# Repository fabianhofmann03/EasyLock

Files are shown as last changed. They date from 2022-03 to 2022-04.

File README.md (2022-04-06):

# EasyLock
EasyLock ist ein Schulprojekt von mir und 2 weiteren Kollegen.
Es nutzt einen magnetischen Schieberiegler der die Tür auf und zu sperrt und einen Hallsensor um den aktuellen Zustand der Tür zu erkennen.
Über eine App auf dem Handy kann das Schloss dann geöffnet, das Passwort geändert oder die Werte des Hallsensors konfiguriert werden.

# Protokoll

Das Projekt nutzt 4 verschiedene Nachrichten zum kommunizieren. Commands, Requests, Data und Status. 
Die ersten Bytes der Nachrichten bestehen aus den Indikatoren, die dem Programm sagen, was für eine Nachricht gesendet wurde. 
Am Ende jeder Nachricht wird ein Control Byte gesendet, das aus allen vorherigen Bytes der Nachricht, welche mit einer Bitweisen XOR Operation kombiniert wurden, besteht. 

## Command

| Command Protocol | | | | | | | | |
|---|---|---|---|---|---|---|---|---|
| Byte Name | Bit 8 | Bit 7 | Bit 6 | Bit 5 | Bit 4 | Bit 3 | Bit 2 | Bit 1 |
| Command Start | 1 | 0 | 0 | 0 | 0 | 0 | 0 | 1 |
| Command | x | x | x | x | x | x | x | x |
| Control Byte | x | x | x | x | x | x | x | x |

Der Command startet im Microcontroller eine Reihe an Befehlen die ausgeführt werden. Während des Befehls werden zwischen App und Microcontroller einige Request- und Data-Nachrichten ausgetauscht. Da der Microcontroller nur einen gewissen Speicherplatz hat, schickt dieser immer erst die Request, wenn er den Wert auch benötigt. Desshalb muss während dem Ausführen der Commands auch eine konstante Verbindung zwischen den Geräten herrschen.

Das zweite Byte besteht aus dem Command, der ausgeführt werden soll. Die Liste an ausführbaren Commands finden Sie hier:

| Command Byte | | | | | | | | | |
|---|---|---|---|---|---|---|---|---|---|
| Command | Bit 8 | Bit 7 | Bit 6 | Bit 5 | Bit 4 | Bit 3 | Bit 2 | Bit 1 | Description |
| Change Password | 0 | 0 | 0 | 0 | 0 | 0 | 0 | 1 | Change the Password of the Lock |
| Open Lock | 0 | 0 | 0 | 0 | 0 | 0 | 1 | 0 | Open the Lock |
| Start Config | 0 | 0 | 0 | 0 | 0 | 0 | 1 | 1 | Starts configuration of Hall Sensor |

## Request und Data

| Request Protocol | | | | | | | | |
|---|---|---|---|---|---|---|---|---|
| Byte Name | Bit 8 | Bit 7 | Bit 6 | Bit 5 | Bit 4 | Bit 3 | Bit 2 | Bit 1 |
| Request Start | 0 | 1 | 0 | 0 | 0 | 0 | 1 | 0 |
| Requested Variable | x | x | x | x | x | x | x | x |
| Control Byte | x | x | x | x | x | x | x | x |

Bei der Request wird von einem der Geräte ein Wert oder manchmal auch nur eine Status-Nachricht gewünscht.
Bei "Password" und "New Password" wird eine Data-Nachricht geschickt zurückgeschickt, bei "Lock Status" eine Status Nachricht.

Das zweite Byte besteht aus der Variable, die gewünscht wird. Dabei ist jedoch das höchstwertige Bit leer zu halten, da das das Flag Bit ist, das verwendet wird um zu erkennen, ob eine neue Request eingetroffen ist. Die Liste an Variablen finden am Ende dieses Abschnitts.

| Data Protocol | | | | | | | | |
|---|---|---|---|---|---|---|---|---|
| Byte Name | Bit 8 | Bit 7 | Bit 6 | Bit 5 | Bit 4 | Bit 3 | Bit 2 | Bit 1 |
| Data Start | 0 | 0 | 1 | 0 | 0 | 1 | 0 | 0 |
| Sent Variable | x | x | x | x | x | x | x | x |
| Data Length | x | x | x | x | x | x | x | x |
| Data | x | x | x | x | x | x | x | x |
| | x | x | x | x | x | x | x | x |
| | …… | …… | …… | …… | …… | …… | …… | …… |
| Control Byte | x | x | x | x | x | x | x | x |

Die Data-Nachricht versendet große Daten die für die Commads benötigt werden. Wegen des begrenzten Speichers des Microcontrollers wird die Länge auf 127 Bytes beschränkt. 

Im zweiten Byte ist gespeichert, welche Variable geschickt wurde. Wie bei der Request Nachricht ist das höchstwertige Bit leer zu halten. Die möglichen Variablen finden Sie am Ende dieses Abschnitts.
Im dritten Byte ist gespeichert, wie viele Bytes an Daten geschickt werden. 
In den folgenden Bits sind dann die Daten gespeichert.

| Variable Name | | | | | | | | | |
|---|---|---|---|---|---|---|---|---|---|
| Variable Name | Bit 8 | Bit 7 | Bit 6 | Bit 5 | Bit 4 | Bit 3 | Bit 2 | Bit 1 | Function |
| Password | 0 | 0 | 0 | 0 | 0 | 0 | 0 | 1 | Current Password of the lock |
| New Password  | 0 | 0 | 0 | 0 | 0 | 0 | 1 | 0 | New Password for the lock |
| Lock Status | 0 | 0 | 0 | 0 | 0 | 0 | 1 | 1 | Status of the Lock |

## Status

| Status Protocol | | | | | | | | |
|---|---|---|---|---|---|---|---|---|
| Byte Name | Bit 8 | Bit 7 | Bit 6 | Bit 5 | Bit 4 | Bit 3 | Bit 2 | Bit 1 |
| Status Start | 0 | 0 | 0 | 1 | 1 | 0 | 0 | 0 |
| Status Message | x | x | x | x | x | x | x | x |

Die Status Nachricht ist eine kurze Nachricht, welche keine spezielle Funktion hat. Beispiel hierfür sind Error-Messages, Bestätigungen für erhaltene Commands/Requests/Daten, oder auch aktuellen Status des Schlosses. 

Die Status-Nachricht hat kein Controll Byte, desshalb besteht sie nur aus dem Indikator und der Status Message.
Status-Messages die versendet werden können finden Sie hier: 

| Status Message | | | | | | | | | |
|---|---|---|---|---|---|---|---|---|---|
| Status Name | Bit 8 | Bit 7 | Bit 6 | Bit 5 | Bit 4 | Bit 3 | Bit 2 | Bit 1 | Description |
| Command executed  | 0 | 0 | 0 | 0 | 0 | 0 | 0 | 1 | The wanted command is finished. No more information needed |
| Received | 0 | 0 | 0 | 0 | 0 | 0 | 1 | 0 | Request or data received successfully |
| Deny | 0 | 0 | 0 | 0 | 0 | 0 | 1 | 1 | Command denied |
| Too much data | 0 | 0 | 0 | 0 | 0 | 1 | 0 | 0 | Too much data was sent. Can't process |
| Message corrupted | 0 | 0 | 0 | 0 | 0 | 1 | 0 | 1 | Message was corrupted while sending. Please repeat |
| Lock opened | 0 | 0 | 0 | 0 | 0 | 1 | 1 | 0 | Lock is currently open |
| Lock closed | 0 | 0 | 0 | 0 | 0 | 1 | 1 | 1 | Lock is currently closed |
| Cancel | 0 | 0 | 0 | 0 | 1 | 0 | 0 | 0 | Cancel Command |
| Continue | 0 | 0 | 0 | 0 | 1 | 0 | 0 | 1 | Continue Command |

## Kommunikation

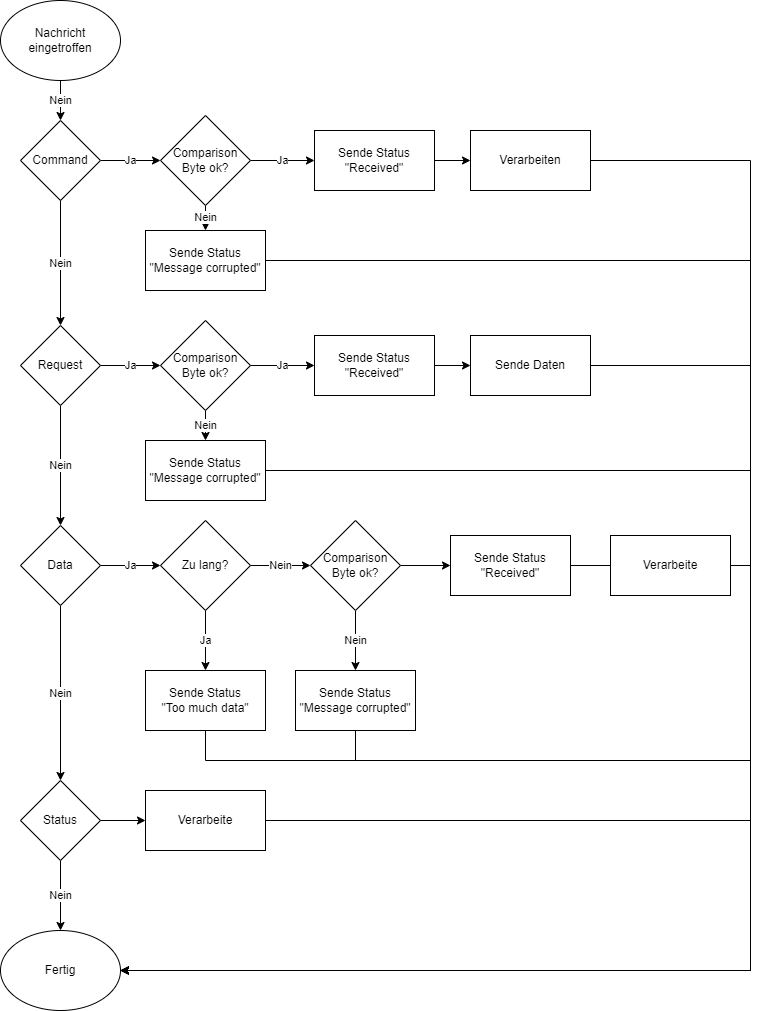
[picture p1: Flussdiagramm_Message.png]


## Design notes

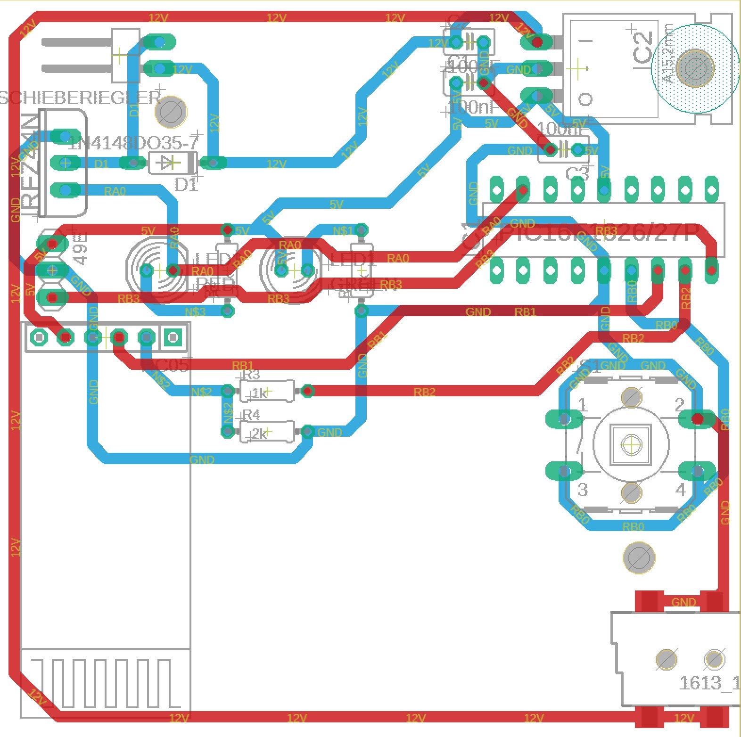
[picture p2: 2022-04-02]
Schaltung & Platine/Platine.jpg

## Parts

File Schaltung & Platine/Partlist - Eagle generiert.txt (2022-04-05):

Partlist

Exported from EasyLock.brd at 05.04.2022 14:36

EAGLE Version 9.6.2 Copyright (c) 1988-2020 Autodesk, Inc.

Assembly variant: 

Part           Value          Package      Library      Position (mm)         Orientation

49E                           1X03         pinhead      (5.08 44.45)          R270
C1             100nF          C025-025X050 rcl          (44.45 62.23)         R0
C2             100nF          C025-025X050 rcl          (44.45 66.04)         R0
C3             100nF          C025-025X050 rcl          (53.34 55.88)         R180
D1             1N4148DO35-7   DO35-7       diode        (16.51 54.61)         R180
HC05                          1X06         HC05         (10.16 38.1)          R180
IC1            PIC16F1826/27P DIL18        microchip    (57.15 48.26)         R0
IC2                           78XXL        v-reg        (54.61 63.5)          R270
IRFZ44N                       TO-220       IRFZ44N      (6.35 54.61)          R90
LED1           GREEN          LED5MM       led          (27.94 44.45)         R0
LED2           RED            LED5MM       led          (15.24 44.45)         R0
R1             1k             0204/7       rcl          (34.29 44.45)         R90
R2             1k             0204/7       rcl          (21.59 44.45)         R90
R3             1k             0204/7       rcl          (25.4 33.02)          R0
R4             2k             0204/7       rcl          (25.4 29.21)          R0
S1                            B3F-40XX     switch-omron (59.69 27.94)         R0
SCHIEBERIEGLER                1X02/90      pinhead      (11.43 64.77)         R90
X1             1613_14        1613_14      con-lumberg  (72.546028125 7.704575) R90

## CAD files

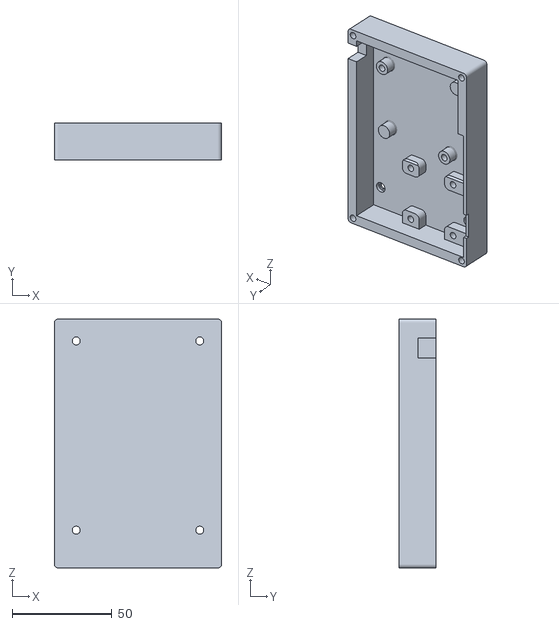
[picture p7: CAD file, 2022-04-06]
3D-Druck Dateien/gehäuse.stl
84.0 x 18.6 x 125.0

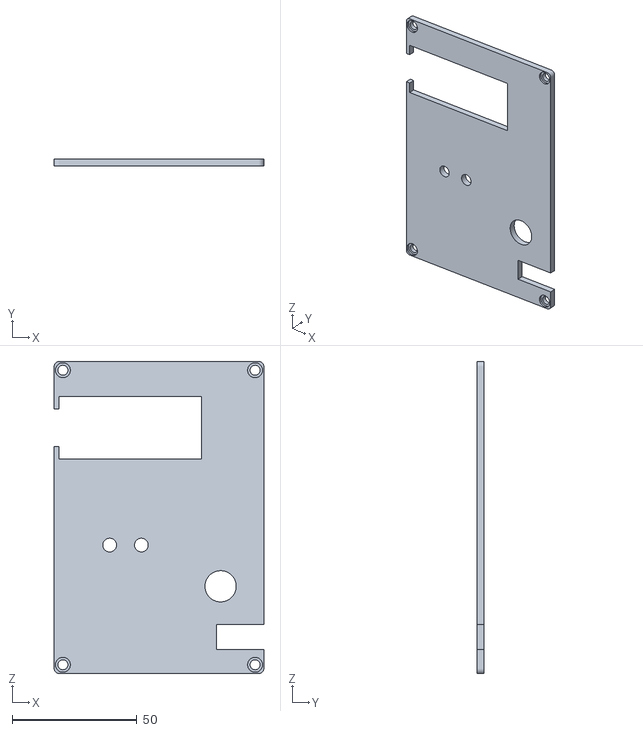
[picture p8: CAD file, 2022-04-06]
3D-Druck Dateien/deckel.stl
84.0 x 3.00 x 125.0

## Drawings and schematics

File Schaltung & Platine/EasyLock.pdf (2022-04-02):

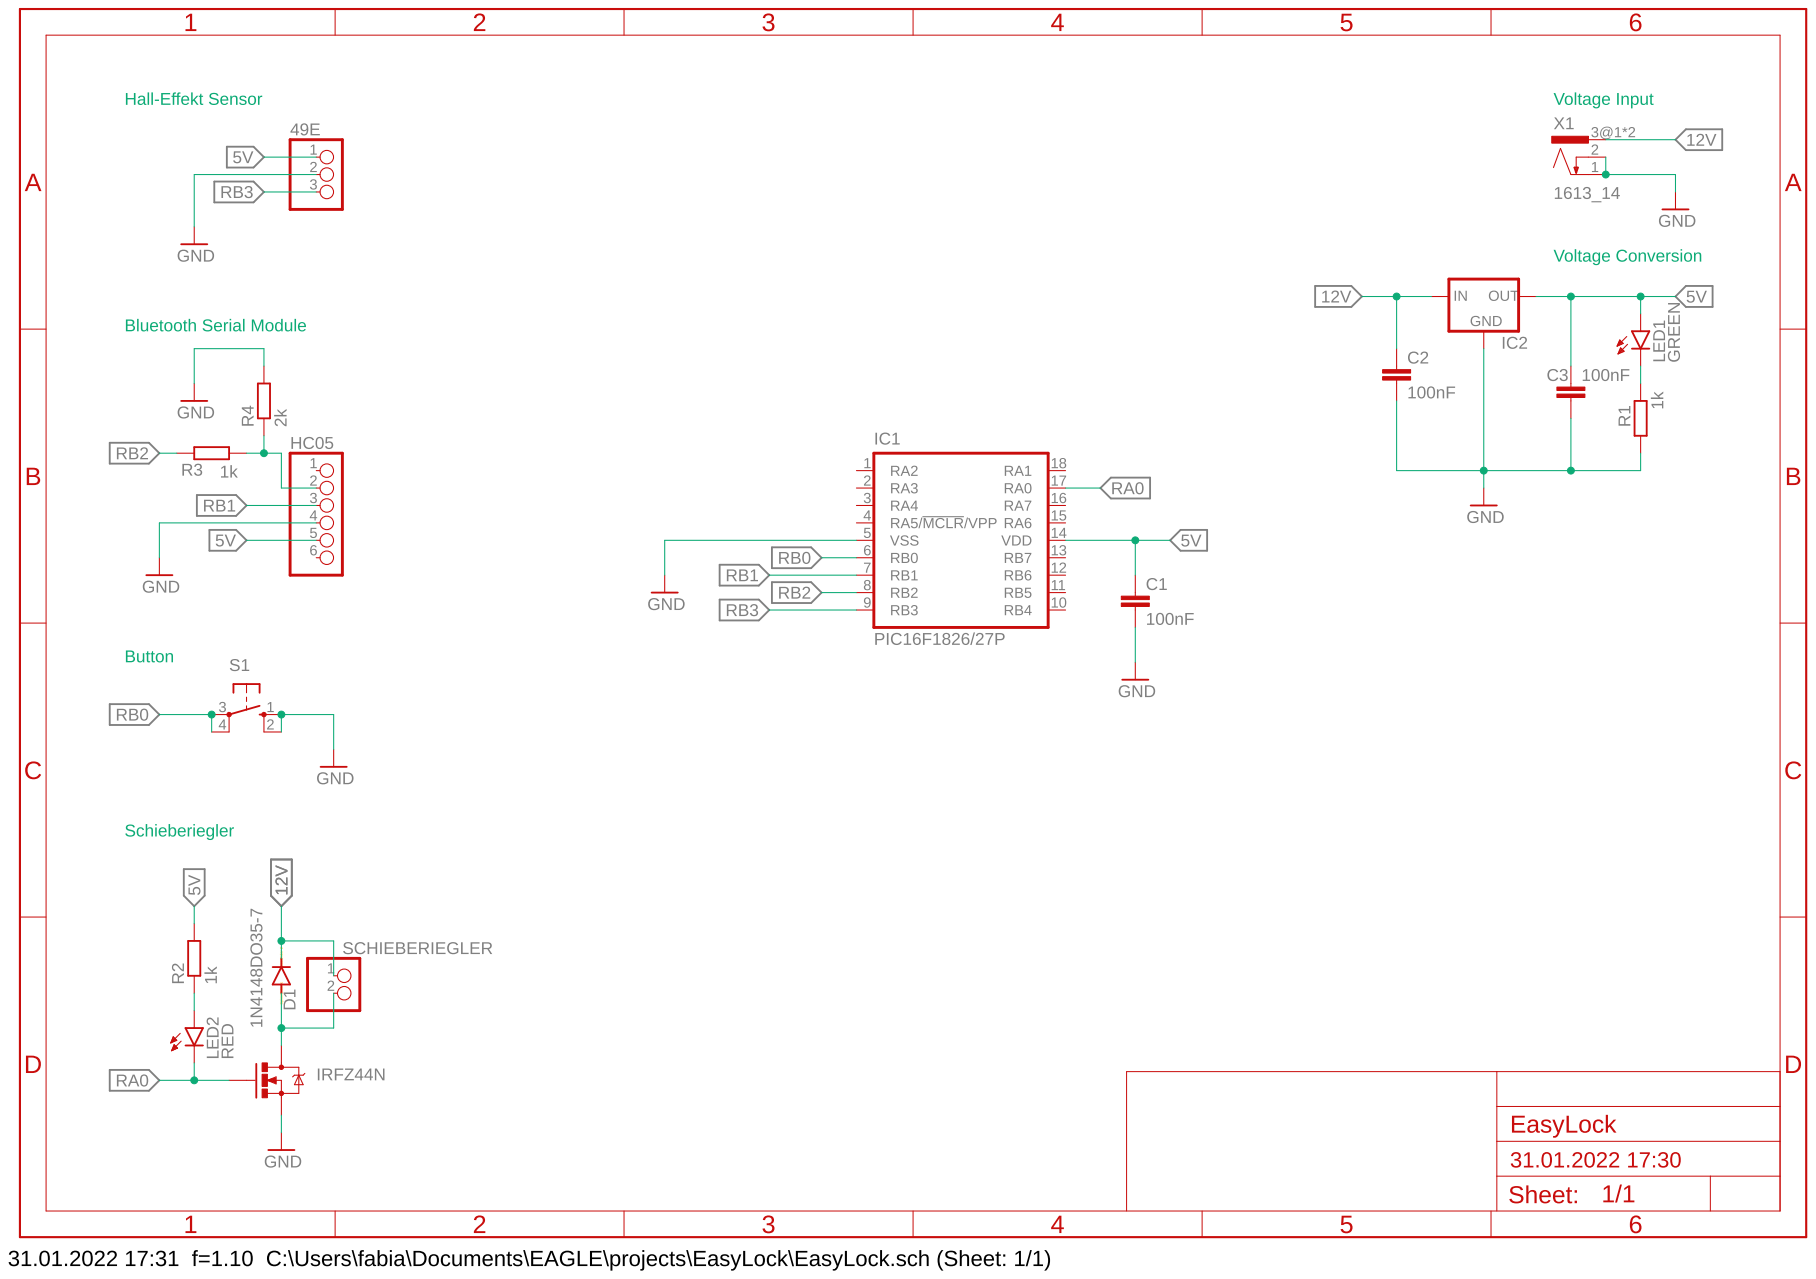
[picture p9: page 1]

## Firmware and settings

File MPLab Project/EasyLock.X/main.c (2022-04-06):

/**
  Generated Main Source File

  Company:
    Microchip Technology Inc.

  File Name:
    main.c

  Summary:
    This is the main file generated using PIC10 / PIC12 / PIC16 / PIC18 MCUs

  Description:
    This header file provides implementations for driver APIs for all modules selected in the GUI.
    Generation Information :
        Product Revision  :  PIC10 / PIC12 / PIC16 / PIC18 MCUs - 1.81.7
        Device            :  PIC16F1827
        Driver Version    :  2.00
 */

/*
    (c) 2018 Microchip Technology Inc. and its subsidiaries. 
    
    Subject to your compliance with these terms, you may use Microchip software and any 
    derivatives exclusively with Microchip products. It is your responsibility to comply with third party 
    license terms applicable to your use of third party software (including open source software) that 
    may accompany Microchip software.
    
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
    IN NO EVENT WILL MICROCHIP BE LIABLE FOR ANY INDIRECT, SPECIAL, PUNITIVE, 
    INCIDENTAL OR CONSEQUENTIAL LOSS, DAMAGE, COST OR EXPENSE OF ANY KIND 
    WHATSOEVER RELATED TO THE SOFTWARE, HOWEVER CAUSED, EVEN IF MICROCHIP 
    HAS BEEN ADVISED OF THE POSSIBILITY OR THE DAMAGES ARE FORESEEABLE. TO 
    THE FULLEST EXTENT ALLOWED BY LAW, MICROCHIP'S TOTAL LIABILITY ON ALL 
    CLAIMS IN ANY WAY RELATED TO THIS SOFTWARE WILL NOT EXCEED THE AMOUNT 
    OF FEES, IF ANY, THAT YOU HAVE PAID DIRECTLY TO MICROCHIP FOR THIS 
    SOFTWARE.
 */

#include "mcc_generated_files/mcc.h"
#include <stdio.h>
#include <stdlib.h>

#define data_storage_size 127
#define password_position 4

#define receive_timer_time 50
#define cmd_timer_time 1000
#define continue_time 12000
#define button_timer_time 50


/*
                         Main application
 */

enum lockstates {
    IDLE, OPENLOCK, WAITFOROPEN, WAITFORCLOSE
};
enum lockstates working_state = IDLE;

enum commandcontroll {
    WAITFORCMD, READCMD, READREQ, READDATLEN, READDATVAR, READDAT, READSTAT, COMP
};
enum commandcontroll cmd_state = WAITFORCMD;

enum commandexecution {
    WAITTOSTART, EXECMD
};
enum commandexecution cmd_exe = WAITTOSTART;

enum command {
    CHANGE_PASSWORD = 1, OPEN_LOCK = 2, START_CONFIG = 3
};

enum variable {
    PASSWORD = 1, NEW_PASSWORD = 2, LOCK_STATUS = 3
};

enum status_message {
    COMMAND_EXECUTED = 1, RECEIVED = 2, DENY = 3, TOO_MUCH_DATA = 4, MESSAGE_CORRUPTED = 5, LOCK_OPEND = 6, LOCK_CLOSED = 7, CANCELD = 8, CONTINUE = 9
};

uint8_t cmd;
uint8_t data_storage[data_storage_size + 2];                //First byte:   [xxxxxxxx]
                                                            //              [x-------] 1: Data completly loaded, 0: Data still loading
                                                            //              [-xxxxxxx] What variable is stored
                                                            //Second byte:  [xxxxxxxx] Length of Data (max 127)

uint8_t request_storage;                                    //  [x-------] 1: Request has come, 0: No request
                                                            //  [-xxxxxxx] Requested Variable

uint8_t status_storage;                                     //  [x-------] 1: State has come, 0: No state
                                                            //  [-xxxxxxx] Last State

uint8_t hall_codes[] = {127, 103};                          // 1: Open door
                                                            // 2: Closed door

int cmd_exe_counter = 0;
bool lock_status = false;

uint8_t new_hall_code_open = 0;
uint8_t new_hall_code_close = 0;

void del_array(uint8_t *array, int16_t len);

void send_msg_stopping(uint8_t *msg, uint8_t len);
void send_cmd(uint8_t cmd);
void send_req(uint8_t var);
void send_dat(uint8_t *dat, uint8_t len, uint8_t var);
void send_stat(uint8_t stat);
bool compare_pw(uint8_t *pw, uint8_t len);
void save_pw(uint8_t *pw, uint8_t len);
void read_hall_codes(void);
void save_hall_codes(uint8_t open, uint8_t close);
bool wait_for_requested(uint8_t req);
void stop_cmd(void);
int seek_confirmation(int wait_num, int continue_num, int retry_num, int cancel_num);
bool door_status_changed(bool open_or_close, int16_t val);

long receive_time = 0;
long receive_timer_len = 0;
long cmd_time = 0;
long cmd_timer_len = 0;
long button_time = 0;
bool button_status = false;
bool button = false;

void timer_up() {
    if(receive_timer_len > 0) receive_time++;
    if(cmd_timer_len > 0) cmd_time++;
    if(button_status) button_time++;
    button = !BUTTON_GetValue();
    if(button != button_status) {
        if(button_status && button_time < button_timer_time) {
            if(lock_status) {
                working_state = WAITFORCLOSE;
            }else {
                working_state = OPENLOCK;
            }
        }else {
            button_time = 0;
        }
    }
    button_status = button;
}

void main(void) {
    // initialize the device
    SYSTEM_Initialize();
    EUSART_Initialize();
    ADC_Initialize();
    TMR2_Initialize();

    // When using interrupts, you need to set the Global and Peripheral Interrupt Enable bits
    // Use the following macros to:

    // Enable the Global Interrupts
    INTERRUPT_GlobalInterruptEnable();

    // Enable the Peripheral Interrupts
    INTERRUPT_PeripheralInterruptEnable();

    ADC_StartConversion();
    TMR2_SetInterruptHandler(timer_up);
    
    read_hall_codes();
    
    while (1) {
        if(receive_timer_len > 0 && receive_time > receive_timer_len) {
            receive_time = 0;
            receive_timer_len = 0;
            stop_cmd();
        }
        if(cmd_timer_len > 0 && cmd_time > cmd_timer_len) {
            send_stat(CANCELD);
            stop_cmd();
        }
        if (EUSART_is_rx_ready()) {
            receive_timer_len = receive_timer_time;
            receive_time = 0;
            uint8_t input = EUSART_Read();
            static uint8_t control_byte;
            static uint8_t data_storage_counter = 0;
            static enum commandcontroll last_state = WAITFORCMD;
            switch (cmd_state) {
                case WAITFORCMD:
                    last_state = cmd_state;
                    if (input == 0b10000001) cmd_state = READCMD;
                    else if (input == 0b01000010) cmd_state = READREQ;
                    else if (input == 0b00100100) cmd_state = READDATVAR;
                    else if (input == 0b00011000) cmd_state = READSTAT;
                    control_byte = input;
                    break;
                case READCMD:
                    cmd = input;
                    last_state = cmd_state;
                    cmd_state = COMP;
                    break;
                case READREQ:
                    request_storage = input;
                    last_state = cmd_state;
                    cmd_state = COMP;
                    break;
                case READDATVAR:
                    data_storage[0] = input;
                    last_state = cmd_state;
                    cmd_state = READDATLEN;
                    break;
                case READDATLEN:
                    data_storage[1] = input;
                    last_state = cmd_state;
                    cmd_state = READDAT;
                    if(data_storage[1] == 0) cmd_state = COMP;
                    break;
                case READDAT:
                    if (data_storage[1] <= data_storage_size) data_storage[data_storage_counter + 2] = input;
                    data_storage_counter++;
                    if (data_storage_counter == (data_storage[1])) {
                        data_storage_counter = 0;
                        last_state = cmd_state;
                        cmd_state = COMP;
                    }
                    break;
                case READSTAT:
                    status_storage = input;
                    last_state = cmd_state;
                    status_storage = status_storage | (1<<7);
                    cmd_state = WAITFORCMD;
                    receive_timer_len = 0;
                    break;
                case COMP:
                    if (control_byte == input) {
                        switch (last_state) {
                            case READCMD:
                                if (control_byte != input) {
                                    send_stat(MESSAGE_CORRUPTED);
                                } else {
                                    stop_cmd();
                                    send_stat(RECEIVED);
                                    cmd_exe = EXECMD;
                                }
                                break;
                            case READREQ:
                                if (control_byte != input) {
                                    send_stat(MESSAGE_CORRUPTED);
                                } else {
                                    send_stat(RECEIVED);
                                    request_storage = request_storage | (1 << 7);
                                }
                                break;
                            case READDAT:
                                if (data_storage[1] > data_storage_size) {
                                    send_stat(TOO_MUCH_DATA);
                                } else if (control_byte != input) {
                                    send_stat(MESSAGE_CORRUPTED);
                                } else {
                                    send_stat(RECEIVED);
                                    data_storage[0] = data_storage[0] | (1 << 7);
                                }
                                break;
                            case READDATLEN:
                                if (data_storage[1] > data_storage_size) {
                                    send_stat(TOO_MUCH_DATA);
                                } else if (control_byte != input) {
                                    send_stat(MESSAGE_CORRUPTED);
                                } else {
                                    send_stat(RECEIVED);
                                    data_storage[0] = data_storage[0] | (1 << 7);
                                }
                                break;
                        }
                    }
                    last_state = cmd_state;
                    cmd_state = WAITFORCMD;
                    receive_timer_len = 0;
                    receive_time = 0;
                    break;
            }
            if (last_state != WAITFORCMD) control_byte = control_byte ^ input;
        }
        
        if((status_storage & (1<<7)) > 0) {
            switch(status_storage & (~(1<<7))) {
                case CANCELD:
                    if(lock_status == true) {
                        ADC_StartConversion();
                        working_state = WAITFORCLOSE;
                    }
                    stop_cmd();
                    status_storage = status_storage & (~(1<<7));
                    break;
            }
        }
        if((request_storage & (1<<7)) > 0) {
            switch(request_storage & (~(1<<7))) {
                case LOCK_STATUS:
                    if(lock_status) {
                        send_stat(LOCK_OPEND);
                    }else {
                        send_stat(LOCK_CLOSED);
                    }
                    request_storage = status_storage & (~(1<<7));
                    break;
            }
        }
        static int old_cmd_exe_counter = 0;
        switch (cmd_exe) {
            case WAITTOSTART:
                    cmd_timer_len = 0;
               break;
            case EXECMD:
                if(old_cmd_exe_counter != cmd_exe_counter) {
                    cmd_time = 0;
                    cmd_timer_len = cmd_timer_time;
                }
                old_cmd_exe_counter = cmd_exe_counter;
                switch (cmd) {
                    case CHANGE_PASSWORD:
                        switch (cmd_exe_counter) {
                            case 0:
                                send_req(PASSWORD);
                                cmd_exe_counter++;
                                break;
                            case 1:
                                cmd_exe_counter = seek_confirmation(1, 2, 0, 255);
                                break;
                            case 2:
                                if(wait_for_requested(PASSWORD)) {
                                    if(compare_pw(&data_storage[2], data_storage[1]) || !BUTTON_GetValue()) {
                                        cmd_exe_counter++;
                                    }else {
                                        send_stat(DENY);
                                        stop_cmd();
                                    }
                                }
                                break;
                            case 3:
                                send_req(NEW_PASSWORD);
                                cmd_exe_counter++;
                                break;
                            case 4:
                                cmd_exe_counter = seek_confirmation(4, 5, 3, 255);
                                break;
                            case 5:
                                if(wait_for_requested(NEW_PASSWORD)) {
                                    save_pw(&data_storage[2], data_storage[1]);
                                    send_stat(COMMAND_EXECUTED);
                                    stop_cmd();
                                }
                                break;
                            case 255:
                                send_stat(CANCELD);
                                stop_cmd();
                                break;
                        }
                        break; 
                    case OPEN_LOCK:
                        switch (cmd_exe_counter) {
                            case 0:
                                if(lock_status == true) {
                                    working_state = WAITFORCLOSE;
                                    send_stat(COMMAND_EXECUTED);
                                    stop_cmd();
                                }else {
                                    send_req(PASSWORD);
                                    cmd_exe_counter++;
                                }
                                break;
                            case 1:
                                cmd_exe_counter = seek_confirmation(1, 2, 0, 255);
                                break;
                            case 2:
                                if(wait_for_requested(PASSWORD)) {
                                    if(compare_pw(&data_storage[2], data_storage[1]) || !BUTTON_GetValue()) {
                                        working_state = OPENLOCK;
                                        send_stat(COMMAND_EXECUTED);
                                    }else {
                                        send_stat(DENY);
                                    }
                                    stop_cmd();
                                }
                                break;
                            case 255:
                                send_stat(CANCELD);
                                stop_cmd();
                                break;
                        }
                        break;
                    
                    case START_CONFIG:
                        switch (cmd_exe_counter) {
                            case 0:
                                send_req(PASSWORD);
                                cmd_exe_counter++;
                                break;
                            case 1:
                                cmd_exe_counter = seek_confirmation(1, 2, 0, 255);
                                break;
                            case 2:
                                if(wait_for_requested(PASSWORD)) {
                                    if(compare_pw(&data_storage[2], data_storage[1]) || !BUTTON_GetValue()) {
                                        working_state = IDLE;
                                        LOCK_SetHigh();
                                        send_stat(LOCK_OPEND);
                                        lock_status = true;
                                        send_stat(CONTINUE);
                                        cmd_exe_counter ++;
                                    }else {
                                        send_stat(DENY);
                                        stop_cmd();
                                    }
                                    
                                }
                                break;
                            case 3:
                                cmd_timer_len = continue_time;
                                if((status_storage & (1<<7)) > 0 && (status_storage & (~(1<<7))) == CONTINUE) {
                                    ADC_StartConversion();
                                    cmd_exe_counter ++;
                                }
                                status_storage = status_storage & (~(1<<7));
                                break;
                            case 4:
                                if(ADC_IsConversionDone()) {
                                    new_hall_code_close = ADC_GetConversionResult();
                                    send_stat(CONTINUE);
                                    cmd_exe_counter ++;
                                }
                                break;
                            case 5:
                                if((status_storage & (1<<7)) > 0 && (status_storage & (~(1<<7))) == CONTINUE) {
                                    ADC_StartConversion();
                                    cmd_exe_counter ++;
                                }
                                status_storage = status_storage & (~(1<<7));
                                break;
                            case 6:
                                if(ADC_IsConversionDone()) {
                                    new_hall_code_open = ADC_GetConversionResult();
                                    send_stat(COMMAND_EXECUTED);
                                    save_hall_codes(new_hall_code_open, new_hall_code_close);
                                    read_hall_codes();
                                    working_state = OPENLOCK;
                                    stop_cmd();
                                    new_hall_code_open = 0;
                                    new_hall_code_close = 0;
                                }
                                break;
                            case 255:
                                send_stat(CANCELD);
                                stop_cmd();
                                new_hall_code_open = 0;
                                new_hall_code_close = 0;
                                break;
                        }
                        break;
                    
                }
                break;
        }

        switch (working_state) {
            case IDLE:
                
                break;
            case OPENLOCK:
                LOCK_SetHigh();
                send_stat(LOCK_OPEND);
                lock_status = true;
                working_state = WAITFOROPEN;
                ADC_StartConversion();
                break;
            case WAITFOROPEN:
                if(ADC_IsConversionDone()) {
                    uint8_t res = ADRESH;
                    if(door_status_changed(true, res)) {
                        working_state = WAITFORCLOSE;
                    }
                    ADC_StartConversion();
                }
                break;
            case WAITFORCLOSE:
                if(ADC_IsConversionDone()) {
                    uint8_t res = ADRESH;
                    if(door_status_changed(false, res)) {
                        send_stat(LOCK_CLOSED);
                        lock_status = false;
                        working_state = IDLE;
                        LOCK_SetLow();
                    }
                    ADC_StartConversion();
                }
                break;
        }
    }
}

void del_array(uint8_t *array, int16_t len) {
    for (int16_t x = 0; x < len; x++) *(array + x) = 0;
}

void send_msg_stopping(uint8_t *msg, uint8_t len) {
    for (int x = 0; x < len; x++) {
        while (!EUSART_is_tx_done());
        EUSART_Write(*(msg + x));
    }
}

void send_cmd(uint8_t cmd) {
    uint8_t command_protocol[] = {0b10000001, cmd, 0};
    command_protocol[2] = command_protocol[0] ^ command_protocol[1];
    send_msg_stopping(command_protocol, 3);
    status_storage = 0;
}

void send_req(uint8_t var) {
    del_array(data_storage, data_storage_size + 2);
    uint8_t request_protocol[] = {0b01000010, var, 0};
    request_protocol[2] = request_protocol[0] ^ request_protocol[1];
    send_msg_stopping(request_protocol, 3);
    status_storage = 0;
}

void send_dat(uint8_t *dat, uint8_t len, uint8_t var) {
    uint8_t control_byte = 0b00100100;
    control_byte = (control_byte ^ len) ^ var;
    send_msg_stopping(0b00100100, 1);
    for (int x = 0; x < len; x++) {
        control_byte = control_byte ^ *(dat + x);
    }
    send_msg_stopping(&len, 1);
    send_msg_stopping(&var, 1);
    send_msg_stopping(dat, len);
    send_msg_stopping(&control_byte, 1);
    status_storage = 0;
}

void send_stat(uint8_t stat) {
    uint8_t status_protocol[] = {0b00011000, stat};
    send_msg_stopping(status_protocol, 2);
}

bool compare_pw(uint8_t *pw, uint8_t len) {
    bool res = true;
    uint8_t eedata = DATAEE_ReadByte(password_position);
    if (eedata != len) {
        res = false;
    } else {
        for (int x = 0; x < len; x++) {
            eedata = DATAEE_ReadByte(x + password_position + 1);
            uint8_t indata = *(pw + x);
            if (eedata != indata) {
                res = false;
                break;
            }
        }
    }
    return res;
}
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

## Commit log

2022-03-31 commit message
    [app_bar_main.xml, app_widget_background.xml, app_widget_inner_view_background.xml]
2022-03-31 Data-Sturktur verändert, Layout angepasst, Bluetooth
    Data-Nachricht Struktur wurde verändert. Kann theoretisch bis zu 255 Zeichen enthalten, wird trotzdem wegen Microcontroller auf 127 gekürzt.
    Layout Farben wurden verändert
    Bluetooth Rechtsstreit wurde verhindert
    [app_bar_main.xml, app_widget_background.xml, app_widget_inner_view_background.xml]
